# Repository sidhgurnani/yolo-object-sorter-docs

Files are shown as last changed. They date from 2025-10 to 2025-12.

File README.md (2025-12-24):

# YOLO-Based Binary Object Sorting System Documentation and Code

## Introduction/Motivation
When a bullet is fired at a crime scene it leaves behind a casing and the bullet itself. The bullet size varies depending on the gun that is being used, but each bullet contains a unique identification that can be traced back to a specific gun that it was fired with. There is currently a relatively outdated process in place, whereby an examiner will have to manually measure and identify markings. While more advanced versions of this technique can be used (standards determined by NIST), it still heavily relies on an examiner going through. While human input can be deemed necessary, it is an inefficient process that can be streamlined if the bullets were able to be somehow pre-sorted. This would save time and make the process more efficient. 
  
Designing a new device would also require engineers to justify the need for such a product, and also delve into how it can be used in other applications. There are similar existing problems in other applications. An example of such an application would be coin sorting. If there were 1000 assorted coins of differing currencies, it would be possible to sort by hand albeit through a lengthy procedure. Another example is in an agricultural setting, where one would have to maybe sort through 2-3 different types of beans efficiently. Other examples include but are not limited to: various assorted electrical components (resistors, op-amps, capacitors, etc), assorted LEGOs, and assorted perler beads. 

## Goals for this GitHub page:
The goal for this GitHub website is to provide updates about my status on this project as they had happened in real-time, including concepts that I had considered, but ultimately did not work out.

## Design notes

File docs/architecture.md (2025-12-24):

## Software Considerations

Early in the project timeline, the focus for any architectural decisions was heavily biased towards the software, as there are many possibilities for the software, and significantly fewer physical prototype solutions. 

### Early Software Decisions

Given that the project solution requires a cyberphysical system, it is best to work with some kind of microcontroller. In addition, since laptops can vary with processing power, age, graphics performance, etc, it is best to utilize a solution that is lighter on a laptop. The goal here is to have as many devices as possible be able to run the software. 

This is where the first major pathway to a solution arrives: using WebUSB. WebUSB is an API that allows certain compatible microcontrollers to be able to communicate to a web browser. This would open up the potential for users to be able to interact with the Arduino using an HTML file. Keeping this solution on a web browser would be able to allow the system to run much lighter.

Such a solution can be seen with [Google's Tiny Sorter](https://experiments.withgoogle.com/tiny-sorter/view/), which is primarily used as a teaching tool to help people learn about computer vision and sorting. One of the main drawbacks about this solution is that it doesn't accomodate for a variety of object types, and would be difficult to sort larger and heavier objects. It also does not allow a user to input a pretrained model, and instead relies on the end user to train the system. If done improperly, or in bad lighting, then the model produced is not as accurate.

This led me down a rabbit hole of using WebUSB and getting my hands on an Arduino Leonardo, which is a WebUSB-compatible Arduino. My findings about WebUSB are laid out in more detail [here](WebUSB_Findings.md). Note that this page can also be found by navigating via the development section, so you can view it then as well.

Long story short, WebUSB is not ideal (from a simplicity point of view) due to the communication protocol that needs to be put in place. With any webpage, a client and server is needed. However, this communication would have to be extended to the Arduino as well. With a large amount of communication happening between the user, client, server, and Arduino, there is bound to be a loss of data somewhere due to data being sent and recieved from multiple sources, essentially overloading the system. While the ideal scenario would be to run something like this, my prototype will not be using a web-based system to reduce the complexity of communicating information. 

### Final Software Decisions

Based on the information outlined above, I have chosen to run the program locally. A graphical user interface (GUI) will be built via Python, which will also handle communication to and from the Arduino via a serial communication port. 

The GUI will allow the user to dictate what gets done and when as well as monitor the whole system and provide that information to the user. A GUI can be constructed in many ways, however, I have chosen to use tkinter for Python. 

Communication to and from the Arduino via a serial communication port is a good option as it allows data to be sent to and from using one channel, whereas using WebUSB would mean data has to transfer from client to server to Arduino. 

More technical details can be seen on the development pages, where the software versions are outlined as I iterate through them towards a working solution. 

## Prototype Considerations

### Early Prototype Decisions

Early on, the choice had to be made to decide whether to design a prototype that works well with one kind of object or womething that won't work as well but can support a varierty of objects. 

Initially, I thought about going with the former. Coins are something that a lot of people have at their homes, including myself, and I thought testing using that would be great. I had initially wanted to design a system that works really well with coins, but coins only. However, it is more ideal to use a system that can support a variety of objects, even at reduced ability and capacity, as it allows for a proper proof of concept to be established with a relatively universal solution.

There are more things that need to be figured out before designing any prototype:

* How are objects fed into system?
* What happens if the user cannot feed objects one-by-one? How does the system handle this?
* How can the system detect the objects in a webcam? Should a box be built around the webcam and an LED to illuminate it or is there another solution?
* What mode of movement should objects use when sending an object to the webcam and from the webcam to the bin?
* etc...

### Final Prototype Decisions

Here are some answers to some of the questions I posed above:

* **How are objects fed into system?** &rarr; They can be fed one by one or ideally, through some kind of feeder, either vibration based or centrifugal.
* **What happens if the user cannot feed objects one-by-one? How does the system handle this?** &rarr; Using something like a feeder can allow objects to be fed more uniformly, regardless of how the user would load the objects.
* **How can the system detect the objects in a webcam? Should a box be built around the webcam and an LED to illuminate it or is there another solution?** &rarr; Two options can be considered: 1. creating a custom enclosure around the webcam with a light that will hopefully detect objects, or 2. using a mirror to angle the view of the webcam downward and create a 3D printed conveyor belt. 
* **What mode of movement should objects use when sending an object to the webcam and from the webcam to the bin?** &rarr; Two options can be considered: 1. Using a relatively universal rail that could transfer objects via a rail 2. perhaps this can be done with a 3D printed conveyor belt, with bins being put on the side of the conveyor belt for easy object sorting via motors or something built into the belt itself.

Update (Nov 2025):

* Note that I answered the questions with what concepts I had in mind at that time, which did not line up 100% with the concept that I ended up going with. The questions and answers were more posed to generate thinking on my side. The answers to the questions were nonbinding at the time, and ended up differing from what the final prototype looked like.

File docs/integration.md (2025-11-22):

As with any cyber physical system, the integration between the software and hardware used is very crucial. Most of the integration took place in parallel with the development, as the Arduino was a key part of the software development. This section will focus on the bridge between the software and the hardware, which is the YOLO model itself.

Technically speaking, there are a few items which can be seen as connecting a physical device to the software. The serial communication protocol and the USB cable are just two such examples. However, the item that makes or breaks how well this entire system works is the YOLO model.

I initially thought that the system was 'plug and play', however, that could not be further from the truth, which is why I have a dedicated page on training models for this system. Note that it has some general training information for all YOLO models, but it is written with this project in mind.

Another page is dedicated to troubleshooting. If one chooses to replicate this project and faces issues, refer to the troubleshooting guide to work through some of the issues. Note that all issues may not be encompassed as I was the main end user of this prototype, so I could not replicate all issues.

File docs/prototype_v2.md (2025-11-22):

The focus for this page will be new concept path that I am going down. As a reminder, below is the concept image I had drafted when decided to go down this path of development (Note that this is the same one that appears on the Prototype Development Main Page): 

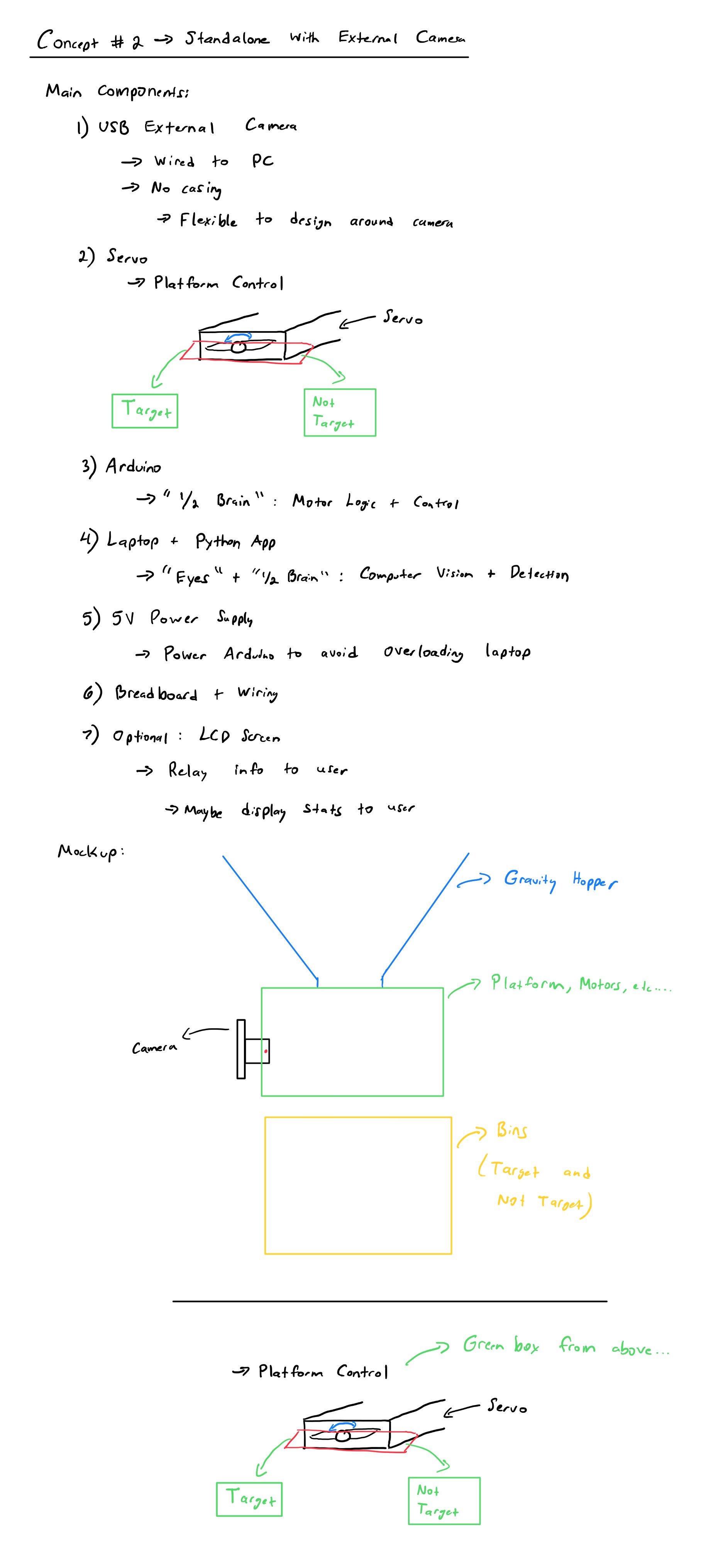
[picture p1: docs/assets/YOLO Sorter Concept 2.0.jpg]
Concept Sketch for Version 2.X


Note that there are a few changes from the concept image to the prototype:

1. **No inclusion of a gravity hopper:** As mentioned a few times across the documentation, object feeding can be considered more of a feature that is nice to have, rather than a requirement for the prototype. In addition, developing a system to feed any kind of objects that have the same relative volume is something more challenging than initially expected. Thus, it makes the most sense to focus on the object detection and sorting more than the feeding into the system, as objects can be manually fed.

2. **LCD Screen is included:** Above, an LCD screen was listed as an optional feature, however, I have decided to include it on the design. One thing to note is that the LCD working is considered lower priority as it is not important to have that working for the prototype to work.

3. **Camera Orientation:** On the concept image, the camera orientation is mounted such that objects would fall into view from up to down and along gravity and the camera would be mounted somewhere on the side to be able to see the object. Upon further reflection, it makes more sense to have the camera be top mounted. This is down to the fact that flat objects such as coins can be made more visible from above, and it won't impact the camera's ability to view other classes of objects. In hindsight, this orientation change helped, as the camera sourced for this project is very zoomed in and has a narrow FOV, which meant I had to mount the camera about 7 inches from the viewing platform. This would not have been possible if I had mounted the camera to face sideways instead of looking down at the objects. 

## Version 2.1

Below is a table of components (not including those in CAD) that need to be integrated. Note that prices are listed in USD and are reflective of those found in early October 2025. 

| Component | Picture | Estimated Unit Cost (on Amazon) |
|---|---|---|
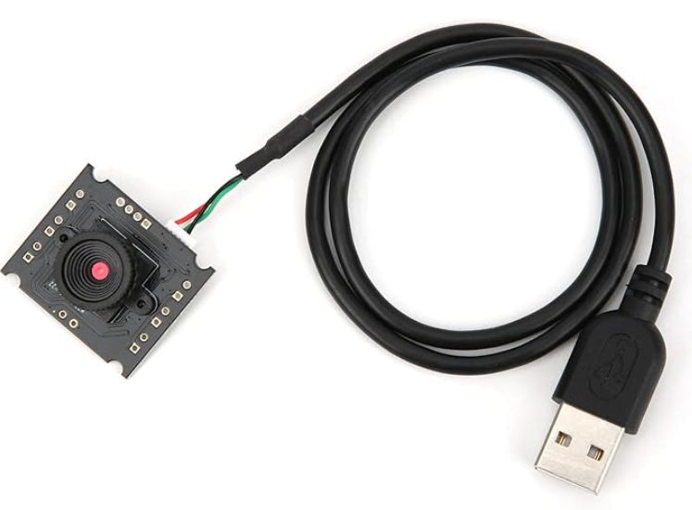
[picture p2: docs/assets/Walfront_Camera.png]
| Walfront USB Camera Module, HBV-W202012HD |  | ~$11-12 |
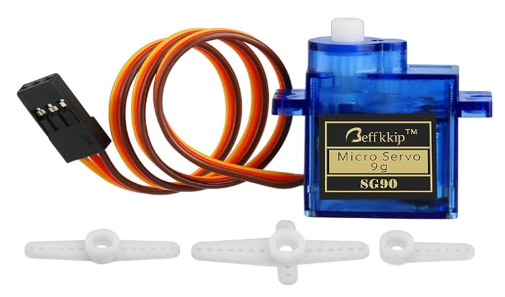
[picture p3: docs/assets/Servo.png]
| MicroServo 9G (SG90) |  | ~$2 (comes in a 4 pack for ~$8) |
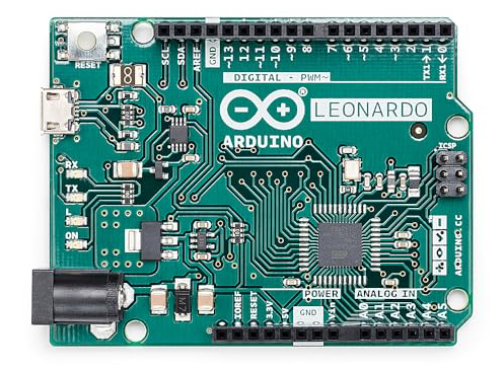
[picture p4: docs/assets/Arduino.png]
| Arduino Leonardo<br/> (**NOTE:** Any microcontroller can be used as long as it meets your requirements) |  | ~$25 | 
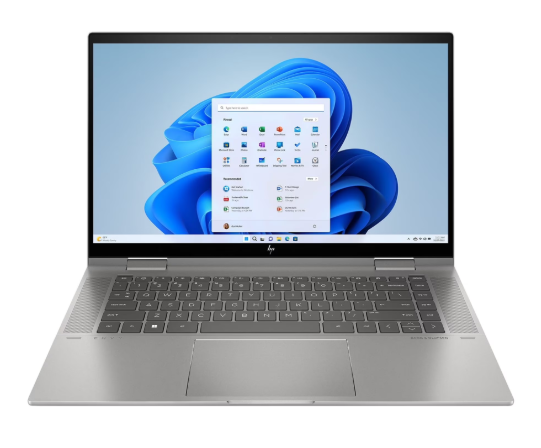
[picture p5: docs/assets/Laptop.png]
| Laptop<br/> (**NOTE:** Laptop must be able to run Python and YOLO, which requires either a decently strong CPU and/or a dedicated GPU. I have the HP ENVY x360 2-in-1 Laptop 15-ew1xxx.)<br/> See Geekbench [here](https://browser.geekbench.com/v5/cpu/22137005) for detailed info about my laptop's specs. |  | ~$800 | 
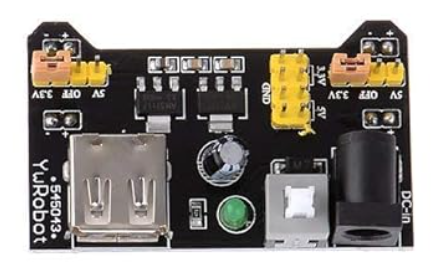
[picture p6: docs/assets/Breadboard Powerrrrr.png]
| 3.3V/5V Breadboard Power Supply Module |  | ~$1.80 (comes in a 5 pack for ~9) | 
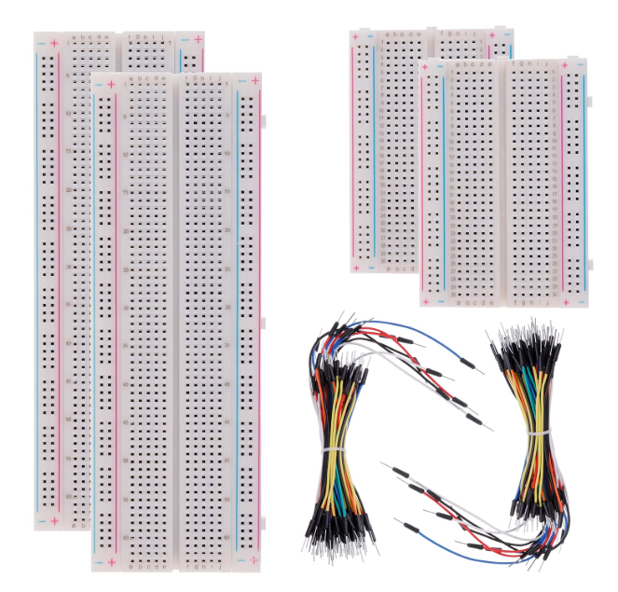
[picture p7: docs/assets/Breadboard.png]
| Breadboard and Jumper Cables (and LEDs if desired) |  | ~$10 (for full pack as pictured) | 
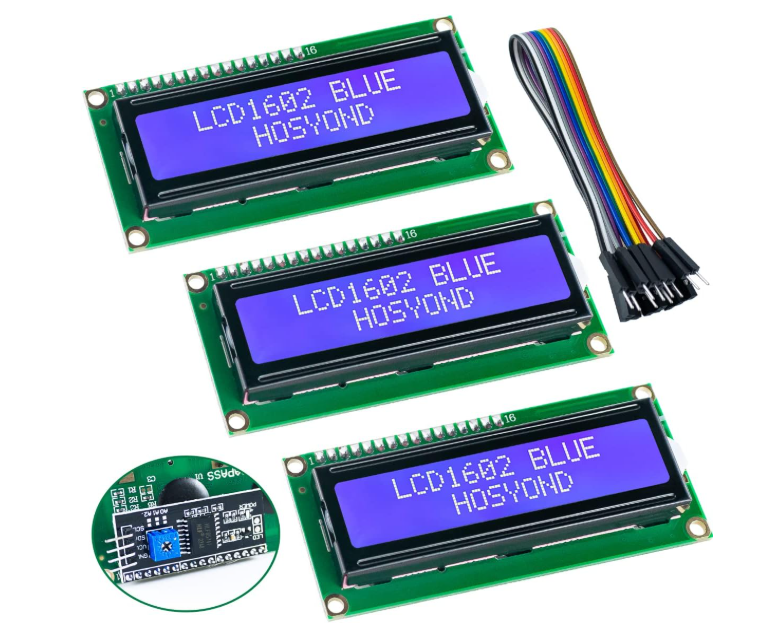
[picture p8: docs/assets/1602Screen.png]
| 1602 LCD Screen |  | ~$4.33 (comes in a 3 pack for ~$13) | 
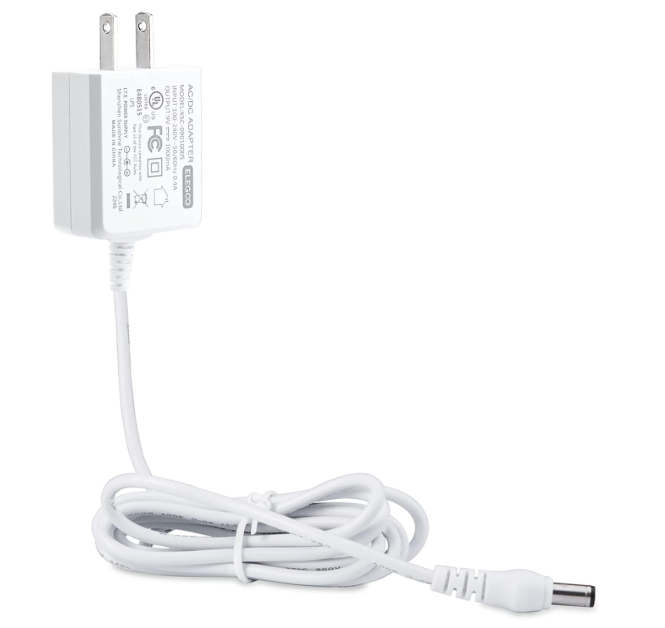
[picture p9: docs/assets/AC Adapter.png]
| AC Adapter (9V, 1A Output) |  | ~$8 | 

### Arduino/Microcontroller Pin Usage

An Arduino Leonardo has a total of 12 Digital Pins (7 of which are PWM) and 6 Analog Pins. Before thinking about the CAD, it is important to see how many pins are used for what is listed above. This provides a good baseline and is able to inform future improvements. 

[Click to view a great article that details information about the Arduino Leonardo and its pins.](https://www.etechnophiles.com/leonardo-pinout-schematic-and-specifications/)

| Electrical Component | Description | Pins required on Arduino |
|---|---|---|
| Green LED | Lets user know that an object can be fed into the system for sorting | 1 Digital PWM Pin |
| Red LED | Lets user know that an object can NOT be fed into the system for sorting | 1 Digital PWM Pin |
| Servo | Rotates platform to send object to target or not target bin | 1 Digital PWM Pin | 
| LCD Screen | Lets user know status of system without having to look at Python interface; Displays stats to user at the end of sorting session | 6 Digital Pins |

One of the things I was initially considering was including a gate to physically stop objects from being fed, however that is not necessary on the prototype. Ultimately, I picked including a screen over a gate, due to constraints on pins. This can be considered another improvement that would be nice to have. 

Since most of the pins left are analog pins, this leaves room to include any sensors that may be needed should the information from the camera not be enough for the system to work properly.

### CAD

I used Onshape to create the CAD for this prototype, and you can view the CAD by clicking [here](https://cad.onshape.com/documents/56ded4b8e86468a67475ca0c/w/01bca40152a05fd67c7a1a53/e/aa33980481ab51f746d18740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).

**Picture Galleries of CAD:**

Various galleries are below to show more details about the components and subassemblies of the CAD. Click thumbnail to enlarge the images.

Camera Mounting Subassembly: 

<!-- Lightbox overlay for Gallery 1 -->
<div id="lightbox1" style="display:none; position:fixed; top:0; left:0; width:100%; height:100%;
  background: rgba(0,0,0,0.9); justify-content:center; align-items:center; z-index:1000; flex-direction: column;">
  <button id="prevBtn1" style="position:absolute; left:20px; top:50%; transform:translateY(-50%); color:white; font-size:2rem; background:none; border:none; cursor:pointer;">&#10094;</button>
  
  <div id="caption1" style="color:white; margin-top:20px; text-align:center; max-width:80%; padding:0 20px;">
    <h3 id="title1" style="margin:10px 0; font-size:1.5rem;"></h3>
    
  </div>
  <button id="nextBtn1" style="position:absolute; right:20px; top:50%; transform:translateY(-50%); color:white; font-size:2rem; background:none; border:none; cursor:pointer;">&#10095;</button>
  <button id="closeBtn1" style="position:absolute; top:20px; right:30px; color:white; font-size:2rem; background:none; border:none; cursor:pointer;">&times;</button>
</div>

<style>
  #gallery1 img.thumb, #gallery2 img.thumb, #gallery3 img.thumb, #gallery4 img.thumb {
    width: 100%;
    height: auto;
    max-width: 200px;
    min-width: 150px;
    cursor: pointer;
    border-radius: 6px;
    transition: transform 0.2s;
    object-fit: cover;
    aspect-ratio: 4/3;
  }

  #gallery1 img.thumb:hover, #gallery2 img.thumb:hover, #gallery3 img.thumb:hover, #gallery4 img.thumb:hover {
    transform: scale(1.05);
  }

  @media (max-width: 600px) {
    #gallery1 img.thumb, #gallery2 img.thumb, #gallery3 img.thumb, #gallery4 img.thumb {
      max-width: calc(50% - 5px);
    }
    #lightbox1 img, #lightbox2 img, #lightbox3 img, #lightbox4 img {
      max-width: 95% !important;
      max-height: 60% !important;
    }
  }

  #prevBtn1, #nextBtn1, #closeBtn1, #prevBtn2, #nextBtn2, #closeBtn2, 
  #prevBtn3, #nextBtn3, #closeBtn3, #prevBtn4, #nextBtn4, #closeBtn4 {
    user-select: none;
  }

  #prevBtn1:hover, #nextBtn1:hover, #closeBtn1:hover,
  #prevBtn2:hover, #nextBtn2:hover, #closeBtn2:hover,
  #prevBtn3:hover, #nextBtn3:hover, #closeBtn3:hover,
  #prevBtn4:hover, #nextBtn4:hover, #closeBtn4:hover {
    opacity: 0.7;
  }
</style>

<script>
document.addEventListener("DOMContentLoaded", () => {
    const galleryDiv1 = document.getElementById('gallery1');
    const lightbox1 = document.getElementById('lightbox1');
    const lightboxImg1 = document.getElementById('lightbox-img1');
    const prevBtn1 = document.getElementById('prevBtn1');
    const nextBtn1 = document.getElementById('nextBtn1');
    const closeBtn1 = document.getElementById('closeBtn1');
    const title1 = document.getElementById('title1');
    const desc1 = document.getElementById('desc1');

    // MODIFY THIS: Add your images with titles and captions
    const images1 = [
        {
            src: "../assets/2.1_Camera_1.png",
            title: "Camera Frame Corner Sleeve (1 of 2)",
            caption: "Four are required. Mounts to top and allows camera frame to slide in and out."
        },
        {
            src: "../assets/2.1_Camera_2.png",
            title: "Camera Frame Corner Sleeve (2 of 2)",
            caption: "Four are required. Mounts to top and allows camera frame to slide in and out."
        },
        {
            src: "../assets/2.1_Camera_Frame_1.png",
            title: "Camera Frame (1 of 5)",
            caption: "Keeps camera steady around 7 inches above viewing platform, with hole to allow lens to go through."
        }, 
        {
            src: "../assets/2.1_Camera_Frame_2.png",
            title: "Camera Frame (2 of 5)",
            caption: "Keeps camera steady around 7 inches above viewing platform, with hole to allow lens to go through."
        }, 
        {
            src: "../assets/2.1_Camera_Frame_3.png",
            title: "Camera Frame (3 of 5)",
            caption: "Keeps camera steady around 7 inches above viewing platform, with hole to allow lens to go through."
        }, 
        {
            src: "../assets/2.1_Camera_Frame_4.png",
            title: "Camera Frame (4 of 5)",
            caption: "Keeps camera steady around 7 inches above viewing platform, with hole to allow lens to go through."
        }, 
        {
            src: "../assets/2.1_Camera_Frame_5.png",
            title: "Camera Frame (5 of 5)",
            caption: "Keeps camera steady around 7 inches above viewing platform, with hole to allow lens to go through."
        },
        {
            src: "../assets/2.1_Top_Plate_1.png",
            title: "Top Plate (1 of 3)",
            caption: "Screws onto frame to hold camera in place. Features a channel for the wired connection to go through."
        }, 
        {
            src: "../assets/2.1_Top_Plate_2.png",
            title: "Top Plate (2 of 3)",
            caption: "Screws onto frame to hold camera in place. Features a channel for the wired connection to go through."
        }, 
        {
            src: "../assets/2.1_Top_Plate_3.png",
            title: "Top Plate (3 of 3)",
            caption: "Screws onto frame to hold camera in place. Features a channel for the wired connection to go through."
        },
        {
            src: "../assets/2.1_Camera_Assembly_1.png",
            title: "Camera Mounting Subassembly (1 of 5)",
            caption: "Camera Mounting Subassembly. Mounted on top of prototype."
        },
        {
            src: "../assets/2.1_Camera_Assembly_2.png",
            title: "Camera Mounting Subassembly (2 of 5)",
            caption: "Camera Mounting Subassembly. Mounted on top of prototype."
        },
        {
            src: "../assets/2.1_Camera_Assembly_3.png",
            title: "Camera Mounting Subassembly (3 of 5)",
            caption: "Camera Mounting Subassembly. Mounted on top of prototype."
        },
        {
            src: "../assets/2.1_Camera_Assembly_4.png",
            title: "Camera Mounting Subassembly (4 of 5)",
            caption: "Camera Mounting Subassembly. Mounted on top of prototype."
        },
        {
            src: "../assets/2.1_Camera_Assembly_5.png",
            title: "Camera Mounting Subassembly (5 of 5)",
            caption: "Camera Mounting Subassembly. Mounted on top of prototype."
        }
    ];

    let currentIndex1 = 0;

    // Load thumbnails
    images1.forEach((img, i) => {
        const thumb = document.createElement('img');
        thumb.src = img.src;
        thumb.className = 'thumb';
        thumb.onclick = () => openLightbox1(i);
        galleryDiv1.appendChild(thumb);
    });

    function openLightbox1(index) {
        currentIndex1 = index;
        lightbox1.style.display = "flex";
        lightboxImg1.src = images1[currentIndex1].src;
        title1.textContent = images1[currentIndex1].title;
        desc1.textContent = images1[currentIndex1].caption;
    }

    function closeLightbox1() {
        lightbox1.style.display = "none";
    }

    function showNext1() {
        currentIndex1 = (currentIndex1 + 1) % images1.length;
        lightboxImg1.src = images1[currentIndex1].src;
        title1.textContent = images1[currentIndex1].title;
        desc1.textContent = images1[currentIndex1].caption;
    }

    function showPrev1() {
        currentIndex1 = (currentIndex1 - 1 + images1.length) % images1.length;
        lightboxImg1.src = images1[currentIndex1].src;
        title1.textContent = images1[currentIndex1].title;
        desc1.textContent = images1[currentIndex1].caption;
    }

    // Navigation
    nextBtn1.onclick = (e) => { e.stopPropagation(); showNext1(); };
    prevBtn1.onclick = (e) => { e.stopPropagation(); showPrev1(); };
    closeBtn1.onclick = closeLightbox1;

    // Close on background click
    lightbox1.onclick = (e) => {
        if (e.target === lightbox1) closeLightbox1();
    };

    // Keyboard controls
    document.addEventListener('keydown', (e) => {
        if (lightbox1.style.display === "flex") {
            if (e.key === "ArrowRight") showNext1();
            if (e.key === "ArrowLeft") showPrev1();
            if (e.key === "Escape") closeLightbox1();
        }
    });
});
</script>

<div><br></div>

Sorting System Subassembly: 

<!-- Lightbox overlay for Gallery 2 -->
<div id="lightbox2" style="display:none; position:fixed; top:0; left:0; width:100%; height:100%;
  background: rgba(0,0,0,0.9); justify-content:center; align-items:center; z-index:1000; flex-direction: column;">
  <button id="prevBtn2" style="position:absolute; left:20px; top:50%; transform:translateY(-50%); color:white; font-size:2rem; background:none; border:none; cursor:pointer;">&#10094;</button>
  
  <div id="caption2" style="color:white; margin-top:20px; text-align:center; max-width:80%; padding:0 20px;">
    <h3 id="title2" style="margin:10px 0; font-size:1.5rem;"></h3>
    
  </div>
  <button id="nextBtn2" style="position:absolute; right:20px; top:50%; transform:translateY(-50%); color:white; font-size:2rem; background:none; border:none; cursor:pointer;">&#10095;</button>
  <button id="closeBtn2" style="position:absolute; top:20px; right:30px; color:white; font-size:2rem; background:none; border:none; cursor:pointer;">&times;</button>
</div>

<script>
document.addEventListener("DOMContentLoaded", () => {
    const galleryDiv2 = document.getElementById('gallery2');
    const lightbox2 = document.getElementById('lightbox2');
    const lightboxImg2 = document.getElementById('lightbox-img2');
    const prevBtn2 = document.getElementById('prevBtn2');
    const nextBtn2 = document.getElementById('nextBtn2');
    const closeBtn2 = document.getElementById('closeBtn2');
    const title2 = document.getElementById('title2');
    const desc2 = document.getElementById('desc2');

    // MODIFY THIS: Add your images with titles and captions
    const images2 = [
        {
            src: "../assets/2.1_Sorting_Cup_1.png",
            title: "Cup (1 of 2)",
            caption: "In CAD for modelling purposes only. Actual cup used is a styrofoam coffee cup with an approx capacity of 12-14 oz."
        },
        {
            src: "../assets/2.1_Sorting_Cup_2.png",
            title: "Cup (2 of 2)",
            caption: "In CAD for modelling purposes only. Actual cup used is a styrofoam coffee cup with an approx capacity of 12-14 oz."
        },
        {
            src: "../assets/2.1_Sorting_Cup_Base_1.png",
            title: "Cup Base (1 of 4)",
            caption: "Two are required. Used to keep base of cup in place."
        }, 
        {
            src: "../assets/2.1_Sorting_Cup_Base_2.png",
            title: "Cup Base (2 of 4)",
            caption: "Two are required. Used to keep base of cup in place."
        }, 
        {
            src: "../assets/2.1_Sorting_Cup_Base_3.png",
            title: "Cup Base (3 of 4)",
            caption: "Two are required. Used to keep base of cup in place."
        }, 
        {
            src: "../assets/2.1_Sorting_Cup_Base_4.png",
            title: "Cup Base (4 of 4)",
            caption: "Two are required. Used to keep base of cup in place."
        },
        {
            src: "../assets/2.1_Sorting_Cup_Drawer_1.png",
            title: "Cup 'Drawer' (1 of 3)",
            caption: "Two are required. Slots used to slide cup back and forth to easily access and empty cup when needed. Counterbore on bottom allows nut to be recessed and not interfere with motion."
        }, 
        {
            src: "../assets/2.1_Sorting_Cup_Drawer_2.png",
            title: "Cup 'Drawer' (2 of 3)",
            caption: "Two are required. Slots used to slide cup back and forth to easily access and empty cup when needed. Counterbore on bottom allows nut to be recessed and not interfere with motion."
        }, 
        {
            src: "../assets/2.1_Sorting_Cup_Drawer_3.png",
            title: "Cup 'Drawer' (3 of 3)",
            caption: "Two are required. Slots used to slide cup back and forth to easily access and empty cup when needed. Counterbore on bottom allows nut to be recessed and not interfere with motion."
        },
        {
            src: "../assets/2.1_Sorting_Cup_Underside_Assembly_1.png",
            title: "Cup Underside Assembly (1 of 2)",
            caption: "NOTE: White 'washer' was printed to ensure bolt would hold everything together."
        }, 
        {
            src: "../assets/2.1_Sorting_Cup_Underside_Assembly_2.png",
            title: "Cup Underside Assembly (2 of 2)",
            caption: "NOTE: White 'washer' was printed to ensure bolt would hold everything together."
        },
        {
            src: "../assets/2.1_Sorting_Platform_1.png",
            title: "Platform (1 of 6)",
            caption: "Object gets fed onto platform and it rotates to either 'Target' or 'Not Target'."
        },
        {
            src: "../assets/2.1_Sorting_Platform_2.png",
            title: "Platform (2 of 6)",
            caption: "Object gets fed onto platform and it rotates to either 'Target' or 'Not Target'."
        },
        {
            src: "../assets/2.1_Sorting_Platform_3.png",
            title: "Platform (3 of 6)",
            caption: "Object gets fed onto platform and it rotates to either 'Target' or 'Not Target'."
        },
        {
            src: "../assets/2.1_Sorting_Platform_4.png",
            title: "Platform (4 of 6)",
            caption: "Object gets fed onto platform and it rotates to either 'Target' or 'Not Target'."
        },
        {
            src: "../assets/2.1_Sorting_Platform_5.png",
            title: "Platform (5 of 6)",
            caption: "Object gets fed onto platform and it rotates to either 'Target' or 'Not Target'."
        },
        {
            src: "../assets/2.1_Sorting_Platform_6.png",
            title: "Platform (6 of 6)",
            caption: "Object gets fed onto platform and it rotates to either 'Target' or 'Not Target'."
        },
        {
            src: "../assets/2.1_Sorting_Ramp_1.png",
            title: "Ramp (1 of 5)",
            caption: "Object is manually fed from top of ramp and it goes down ramp onto platform. Ramp also has a small part to house one end of the platform to ensure platform stability."
        },
        {
            src: "../assets/2.1_Sorting_Ramp_2.png",
            title: "Ramp (2 of 5)",
            caption: "Object is manually fed from top of ramp and it goes down ramp onto platform. Ramp also has a small part to house one end of the platform to ensure platform stability."
        },
        {
            src: "../assets/2.1_Sorting_Ramp_3.png",
            title: "Ramp (3 of 5)",
            caption: "Object is manually fed from top of ramp and it goes down ramp onto platform. Ramp also has a small part to house one end of the platform to ensure platform stability."
        },
        {
            src: "../assets/2.1_Sorting_Ramp_4.png",
            title: "Ramp (4 of 5)",
            caption: "Object is manually fed from top of ramp and it goes down ramp onto platform. Ramp also has a small part to house one end of the platform to ensure platform stability."
        },
        {
            src: "../assets/2.1_Sorting_Ramp_5.png",
            title: "Ramp (5 of 5)",
            caption: "Object is manually fed from top of ramp and it goes down ramp onto platform. Ramp also has a small part to house one end of the platform to ensure platform stability."
        },
        {
            src: "../assets/2.1_Sorting_Servo_Mount_1.png",
            title: "Servo Mount (1 of 5)",
            caption: "Attaches to shell and holds servo in place."
        },
        {
            src: "../assets/2.1_Sorting_Servo_Mount_2.png",
            title: "Servo Mount (2 of 5)",
            caption: "Attaches to shell and holds servo in place."
        },
        {
            src: "../assets/2.1_Sorting_Servo_Mount_3.png",
            title: "Servo Mount (3 of 5)",
            caption: "Attaches to shell and holds servo in place."
        },
        {
            src: "../assets/2.1_Sorting_Servo_Mount_4.png",
            title: "Servo Mount (4 of 5)",
            caption: "Attaches to shell and holds servo in place."
        },
        {
            src: "../assets/2.1_Sorting_Servo_Mount_5.png",
            title: "Servo Mount (5 of 5)",
            caption: "Attaches to shell and holds servo in place."
        },
        {
            src: "../assets/2.1_Sorting_Assembly_1.png",
            title: "Sorting System Subassembly (1 of 7)",
            caption: "Full sorting subassembly images."
        },
        {
            src: "../assets/2.1_Sorting_Assembly_2.png",
            title: "Sorting System Subassembly (2 of 7)",
            caption: "Full sorting subassembly images."
        },
        {
            src: "../assets/2.1_Sorting_Assembly_3.png",
            title: "Sorting System Subassembly (3 of 7)",
            caption: "Full sorting subassembly images."
        },
        {
            src: "../assets/2.1_Sorting_Assembly_4.png",
            title: "Sorting System Subassembly (4 of 7)",
            caption: "Full sorting subassembly images."
        },
        {
            src: "../assets/2.1_Sorting_Assembly_5.png",
            title: "Sorting System Subassembly (5 of 7)",
            caption: "Full sorting subassembly images."
        },
        {
            src: "../assets/2.1_Sorting_Assembly_6.png",
            title: "Sorting System Subassembly (6 of 7)",
            caption: "Full sorting subassembly images."
        },
        {
            src: "../assets/2.1_Sorting_Assembly_7.png",
            title: "Sorting System Subassembly (7 of 7)",
            caption: "Closeup of Platform and how end sits inside ramp."
        },
    ];

    let currentIndex2 = 0;

    // Load thumbnails
    images2.forEach((img, i) => {
        const thumb = document.createElement('img');
        thumb.src = img.src;
        thumb.className = 'thumb';
        thumb.onclick = () => openLightbox2(i);
        galleryDiv2.appendChild(thumb);
    });

    function openLightbox2(index) {
        currentIndex2 = index;
        lightbox2.style.display = "flex";
        lightboxImg2.src = images2[currentIndex2].src;
        title2.textContent = images2[currentIndex2].title;
        desc2.textContent = images2[currentIndex2].caption;
    }

    function closeLightbox2() {
        lightbox2.style.display = "none";
    }

    function showNext2() {
        currentIndex2 = (currentIndex2 + 1) % images2.length;
        lightboxImg2.src = images2[currentIndex2].src;
        title2.textContent = images2[currentIndex2].title;
        desc2.textContent = images2[currentIndex2].caption;
    }

    function showPrev2() {
        currentIndex2 = (currentIndex2 - 1 + images2.length) % images2.length;
        lightboxImg2.src = images2[currentIndex2].src;
        title2.textContent = images2[currentIndex2].title;
        desc2.textContent = images2[currentIndex2].caption;
    }

    // Navigation
    nextBtn2.onclick = (e) => { e.stopPropagation(); showNext2(); };
    prevBtn2.onclick = (e) => { e.stopPropagation(); showPrev2(); };
    closeBtn2.onclick = closeLightbox2;

    // Close on background click
    lightbox2.onclick = (e) => {
        if (e.target === lightbox2) closeLightbox2();
    };

    // Keyboard controls
    document.addEventListener('keydown', (e) => {
        if (lightbox2.style.display === "flex") {
            if (e.key === "ArrowRight") showNext2();
            if (e.key === "ArrowLeft") showPrev2();
            if (e.key === "Escape") closeLightbox2();
        }
    });
});
</script>

<div><br></div>

Body Subassembly:

<!-- Lightbox overlay for Gallery 3 -->
<div id="lightbox3" style="display:none; position:fixed; top:0; left:0; width:100%; height:100%;
  background: rgba(0,0,0,0.9); justify-content:center; align-items:center; z-index:1000; flex-direction: column;">
  <button id="prevBtn3" style="position:absolute; left:20px; top:50%; transform:translateY(-50%); color:white; font-size:2rem; background:none; border:none; cursor:pointer;">&#10094;</button>
  
  <div id="caption3" style="color:white; margin-top:20px; text-align:center; max-width:80%; padding:0 20px;">
    <h3 id="title3" style="margin:10px 0; font-size:1.5rem;"></h3>
    
  </div>
  <button id="nextBtn3" style="position:absolute; right:20px; top:50%; transform:translateY(-50%); color:white; font-size:2rem; background:none; border:none; cursor:pointer;">&#10095;</button>
  <button id="closeBtn3" style="position:absolute; top:20px; right:30px; color:white; font-size:2rem; background:none; border:none; cursor:pointer;">&times;</button>
</div>

<script>
document.addEventListener("DOMContentLoaded", () => {
    const galleryDiv3 = document.getElementById('gallery3');
    const lightbox3 = document.getElementById('lightbox3');
    const lightboxImg3 = document.getElementById('lightbox-img3');
    const prevBtn3 = document.getElementById('prevBtn3');
    const nextBtn3 = document.getElementById('nextBtn3');
    const closeBtn3 = document.getElementById('closeBtn3');
    const title3 = document.getElementById('title3');
    const desc3 = document.getElementById('desc3');

    // MODIFY THIS: Add your images with titles and captions
    const images3 = [
        {
            src: "../assets/2.1_Body_Base_1.png",
            title: "Base (1 of 3)",
            caption: "Provides extra rigidity to overall prototype. Nut sticking out from bottom will go into couterbore holes to allow system to be flush."
        },
        {
            src: "../assets/2.1_Body_Base_2.png",
            title: "Base (2 of 3)",
            caption: "Provides extra rigidity to overall prototype. Nut sticking out from bottom will go into couterbore holes to allow system to be flush."
        },
        {
            src: "../assets/2.1_Body_Base_3.png",
            title: "Base (3 of 3)",
            caption: "Provides extra rigidity to overall prototype. Nut sticking out from bottom will go into couterbore holes to allow system to be flush."
        },
        {
            src: "../assets/2.1_Body_Bottom_1.png",
            title: "Bottom (1 of 3)",
            caption: "Provides mounting points for shell and provides pins for pin-slot mechanism to allow cup 'drawers' to move."
        },
        {
            src: "../assets/2.1_Body_Bottom_2.png",
            title: "Bottom (2 of 3)",
            caption: "Provides mounting points for shell and provides pins for pin-slot mechanism to allow cup 'drawers' to move."
        },
        {
            src: "../assets/2.1_Body_Bottom_3.png",
            title: "Bottom (3 of 3)",
            caption: "Provides mounting points for shell and provides pins for pin-slot mechanism to allow cup 'drawers' to move."
        },
        {
            src: "../assets/2.1_Body_Labels_1.png",
            title: "Bin Label Plates (1 of 1)",
            caption: "Two are used, remain optional to design. Labels bin to avoid confusion. NOTE: Text for labels was added in Bambu Studio (slicing software) and .3mf file is provided later on this page."
        },
        {
            src: "../assets/2.1_Body_LCD_Holder_1.png",
            title: "LCD Screen Frame (1 of 3)",
            caption: "Mounts LCD Screen to shell and provides space to accomodate green and red LEDs."
        },
        {
            src: "../assets/2.1_Body_LCD_Holder_2.png",
            title: "LCD Screen Frame (2 of 3)",
            caption: "Mounts LCD Screen to shell and provides space to accomodate green and red LEDs."
        },
        {
            src: "../assets/2.1_Body_LCD_Holder_3.png",
            title: "LCD Screen Frame (3 of 3)",
            caption: "Mounts LCD Screen to shell and provides space to accomodate green and red LEDs."
        },
        {
            src: "../assets/2.1_Body_Shell_1.png",
            title: "Shell (1 of 7)",
            caption: "Provides height to system, mounting points, and wire routing for servo wires."
        },
        {
            src: "../assets/2.1_Body_Shell_2.png",
            title: "Shell (2 of 7)",
            caption: "Provides height to system, mounting points, and wire routing for servo wires."
        },
        {
            src: "../assets/2.1_Body_Shell_3.png",
            title: "Shell (3 of 7)",
            caption: "Provides height to system, mounting points, and wire routing for servo wires."
        },
        {
            src: "../assets/2.1_Body_Shell_4.png",
            title: "Shell (4 of 7)",
            caption: "Provides height to system, mounting points, and wire routing for servo wires."
        },
        {
            src: "../assets/2.1_Body_Shell_5.png",
            title: "Shell (5 of 7)",
            caption: "Provides height to system, mounting points, and wire routing for servo wires."
        },
        {
            src: "../assets/2.1_Body_Shell_6.png",
            title: "Shell (6 of 7)",
            caption: "Provides height to system, mounting points, and wire routing for servo wires."
        },
        {
            src: "../assets/2.1_Body_Shell_7.png",
            title: "Shell (7 of 7)",
            caption: "Provides height to system, mounting points, and wire routing for servo wires."
        },
        {
            src: "../assets/2.1_Body_Assembly_1.png",
            title: "Body Subassembly (1 of 7)",
            caption: "Pictures of fully assembled body in CAD."
        },
        {
            src: "../assets/2.1_Body_Assembly_2.png",
            title: "Body Subassembly (2 of 7)",
            caption: "Pictures of fully assembled body in CAD."
        },
        {
            src: "../assets/2.1_Body_Assembly_3.png",
            title: "Body Subassembly (3 of 7)",
            caption: "Pictures of fully assembled body in CAD."
        },
        {
            src: "../assets/2.1_Body_Assembly_4.png",
            title: "Body Subassembly (4 of 7)",
            caption: "Pictures of fully assembled body in CAD."
        },
        {
            src: "../assets/2.1_Body_Assembly_5.png",
            title: "Body Subassembly (5 of 7)",
            caption: "Pictures of fully assembled body in CAD."
        },
        {
            src: "../assets/2.1_Body_Assembly_6.png",
            title: "Body Subassembly (6 of 7)",
            caption: "Pictures of fully assembled body in CAD."
        },
        {
            src: "../assets/2.1_Body_Assembly_7.png",
            title: "Body Subassembly (7 of 7)",
            caption: "Pictures of fully assembled body in CAD."
        }
    ];

    let currentIndex3 = 0;

    // Load thumbnails
    images3.forEach((img, i) => {
        const thumb = document.createElement('img');
        thumb.src = img.src;
        thumb.className = 'thumb';
        thumb.onclick = () => openLightbox3(i);
        galleryDiv3.appendChild(thumb);
    });

    function openLightbox3(index) {
        currentIndex3 = index;
        lightbox3.style.display = "flex";
        lightboxImg3.src = images3[currentIndex3].src;
        title3.textContent = images3[currentIndex3].title;
        desc3.textContent = images3[currentIndex3].caption;
    }

    function closeLightbox3() {
        lightbox3.style.display = "none";
    }

    function showNext3() {
        currentIndex3 = (currentIndex3 + 1) % images3.length;
        lightboxImg3.src = images3[currentIndex3].src;
        title3.textContent = images3[currentIndex3].title;
        desc3.textContent = images3[currentIndex3].caption;
    }

    function showPrev3() {
        currentIndex3 = (currentIndex3 - 1 + images3.length) % images3.length;
        lightboxImg3.src = images3[currentIndex3].src;
        title3.textContent = images3[currentIndex3].title;
        desc3.textContent = images3[currentIndex3].caption;
    }

    // Navigation
    nextBtn3.onclick = (e) => { e.stopPropagation(); showNext3(); };
    prevBtn3.onclick = (e) => { e.stopPropagation(); showPrev3(); };
    closeBtn3.onclick = closeLightbox3;

    // Close on background click
    lightbox3.onclick = (e) => {
        if (e.target === lightbox3) closeLightbox3();
    };

    // Keyboard controls
    document.addEventListener('keydown', (e) => {
        if (lightbox3.style.display === "flex") {
            if (e.key === "ArrowRight") showNext3();
            if (e.key === "ArrowLeft") showPrev3();
            if (e.key === "Escape") closeLightbox3();
        }
    });
});
</script>

<div><br></div>

Full Assembly: 

<!-- Lightbox overlay for Gallery 4 -->
<div id="lightbox4" style="display:none; position:fixed; top:0; left:0; width:100%; height:100%;
  background: rgba(0,0,0,0.9); justify-content:center; align-items:center; z-index:1000; flex-direction: column;">
  <button id="prevBtn4" style="position:absolute; left:20px; top:50%; transform:translateY(-50%); color:white; font-size:2rem; background:none; border:none; cursor:pointer;">&#10094;</button>
  
  <div id="caption4" style="color:white; margin-top:20px; text-align:center; max-width:80%; padding:0 20px;">
    <h3 id="title4" style="margin:10px 0; font-size:1.5rem;"></h3>
    
  </div>
  <button id="nextBtn4" style="position:absolute; right:20px; top:50%; transform:translateY(-50%); color:white; font-size:2rem; background:none; border:none; cursor:pointer;">&#10095;</button>
  <button id="closeBtn4" style="position:absolute; top:20px; right:30px; color:white; font-size:2rem; background:none; border:none; cursor:pointer;">&times;</button>
</div>

<script>
document.addEventListener("DOMContentLoaded", () => {
    const galleryDiv4 = document.getElementById('gallery4');
    const lightbox4 = document.getElementById('lightbox4');
    const lightboxImg4 = document.getElementById('lightbox-img4');
    const prevBtn4 = document.getElementById('prevBtn4');
    const nextBtn4 = document.getElementById('nextBtn4');
    const closeBtn4 = document.getElementById('closeBtn4');
    const title4 = document.getElementById('title4');
    const desc4 = document.getElementById('desc4');

    // MODIFY THIS: Add your images with titles and captions
    const images4 = [
        {
            src: "../assets/2.1_Full_2.png",
            title: "Full Assembly of Version 2.1 (1 of 5)",
            caption: "Fully assembled version in CAD with semi-accurate color to filament being used to 3D print it."
        },
        {
            src: "../assets/2.1_Full_3.png",
            title: "Full Assembly of Version 2.1 (2 of 5)",
            caption: "Fully assembled version in CAD with semi-accurate color to filament being used to 3D print it."
        },
        {
            src: "../assets/2.1_Full_4.png",
            title: "Full Assembly of Version 2.1 (3 of 5)",
            caption: "Fully assembled version in CAD with semi-accurate color to filament being used to 3D print it."
        },
        {
            src: "../assets/2.1_Full_5.png",
            title: "Full Assembly of Version 2.1 (4 of 5)",
            caption: "Fully assembled version in CAD with semi-accurate color to filament being used to 3D print it."
        },
        {
            src: "../assets/2.1_Full_1.png",
            title: "Full Assembly of Version 2.1 (5 of 5)",
            caption: "Fully assembled version in CAD with semi-accurate color to filament being used to 3D print it."
        }
    ];

    let currentIndex4 = 0;

    // Load thumbnails
    images4.forEach((img, i) => {
        const thumb = document.createElement('img');
        thumb.src = img.src;
        thumb.className = 'thumb';
        thumb.onclick = () => openLightbox4(i);
        galleryDiv4.appendChild(thumb);
    });

    function openLightbox4(index) {
        currentIndex4 = index;
        lightbox4.style.display = "flex";
        lightboxImg4.src = images4[currentIndex4].src;
        title4.textContent = images4[currentIndex4].title;
        desc4.textContent = images4[currentIndex4].caption;
    }

    function closeLightbox4() {
        lightbox4.style.display = "none";
    }

    function showNext4() {
        currentIndex4 = (currentIndex4 + 1) % images4.length;
        lightboxImg4.src = images4[currentIndex4].src;
        title4.textContent = images4[currentIndex4].title;
        desc4.textContent = images4[currentIndex4].caption;
    }

    function showPrev4() {
        currentIndex4 = (currentIndex4 - 1 + images4.length) % images4.length;
        lightboxImg4.src = images4[currentIndex4].src;
        title4.textContent = images4[currentIndex4].title;
        desc4.textContent = images4[currentIndex4].caption;
    }

    // Navigation
    nextBtn4.onclick = (e) => { e.stopPropagation(); showNext4(); };
    prevBtn4.onclick = (e) => { e.stopPropagation(); showPrev4(); };
    closeBtn4.onclick = closeLightbox4;

    // Close on background click
    lightbox4.onclick = (e) => {
        if (e.target === lightbox4) closeLightbox4();
    };

    // Keyboard controls
    document.addEventListener('keydown', (e) => {
        if (lightbox4.style.display === "flex") {
            if (e.key === "ArrowRight") showNext4();
            if (e.key === "ArrowLeft") showPrev4();
            if (e.key === "Escape") closeLightbox4();
        }
    });
});
</script>

<div><br></div>

### Prototype Production

A total of 5 colors were used throughout the printing process. I am listing the color as well as the brand and type of filament.

1. White (Bambu Lab PLA Basic)
2. Black (Bambu Lab PLA Basic)
3. Light Grey (Bambu Lab PLA Basic)
4. Transparent Red (SUNLU Transparent PLA)
5. Transparent Blue (SUNLU Transparent PLA)

Most of the slicing settings are pretty much left untouched, however, there are some notable settings that I used:

* **Infill Pattern:** Gyroid
* **Infill Density:** 15% (can probably go as low as 7-10%)
* **Wall Loops:** 2
* **Supports:** Normal supports with default settings (not tree supports)

Everything else was left as the default settings found in Bambu Studio.

Below are some details that summarizes all relevant details after slicing in Bambu Studio:

**Total Filament Usage (Including Supports):**

| Color | Filament Used|
|---|---|
| White | 18.76 g |
| Black | 35.00 g |
| Light Grey | 288.22 g |
| Transparent Red | 91.41 g |
| Transparent Blue | 31.82 g |
|  |  |
| **Total** | **465.20 g** |

**Costs:**

Regardless of actual filament, assume that all filament is acquired at the rate of $23/kg, which is similar to how much Bambu Lab PLA Basic filament costs. 

Total Cost = $0.023/g * 465.20 g = **$10.70**

**Time:** 

Total time spent printing is calculated at 13 hours 56 minutes (across 7 plates) according to Bambu Studio using default settings for speed.

### Assembly

Below are a few tables that show a list of components and hardware required:

| 3D Printed Part | Subsystem | Quantity |
|---|---|---|
| Camera Frame Corner Sleeve | Camera Mounting | 4 |
| Camera Frame | Camera Mounting | 1 |
| Top Plate | Camera Mounting | 1 |
| 12-14oz Coffee Cup | Sorting | 2 |
| Cup Base | Sorting | 2 |
| Cup 'Washer' | Sorting | 2 |
| Cup 'Drawer' | Sorting | 2 |
| Platform | Sorting | 1 |
| Ramp | Sorting | 1 |
| Servo Mount | Sorting | 1 |
| Platform | Sorting | 1 |
| Base | Body | 1 |
| Bottom | Body | 1 |
| Bin Label Plates | Body | 2 |
| LCD Screen Frame | Body | 1 |
| Shell | Body | 1 |

| Electrical Component | Quantity | Purpose |
|---|---|---|
| 1602 LCD Scren | 1 | Display key information and statistics to user |
| Green LED | 1 | Tells user object can be fed |
| Red LED | 1 | Tells user objects can NOT be fed |
| 10kΩ Potentiometer | 1 | Controls screen brightness |
| MicroServo 9G (SG90) | 1 | Rotate platform to move object for sorting into 'Target' or 'Not Target' bin |
| Walfront Camera Module | 1 | External USB Camera to provide view of object for YOLO to process |
| Arduino Leonardo | 1 | Communicates back and forth with Python app to perform key functions |
| Breadboard | 1 | Connects Arduino to External Power Source |
| Breadboard Power Supply Module + AC Adapter | 1 | Powers Servo, LCD Screen, and Arduino to take load off of Arduino and Laptop |
| M-M Breadboard Jumper Cables | Many | Creates electrical connection between components, power source, and Arduino pins without soldering |
| F-M Breadboard Jumper Cables | Many | Creates electrical connection between components, power source, and Arduino pins without soldering |

| Quantity x Screw Size | Purpose |
|---|---|
| 4 x M3 | Mounts Shell to Bottom; Threads + Nut Sticking out sits flush with base |
| 2 x M3 | Mounts LCD Screen Frame to Shell |
| 4 x M2 | Mounts 1602 LCD Screen to LCD Screen Frame |
| 2 x M3 | Mount Cup Washer + Cup Base + Cup 'Drawer' |
| 4 x M2 | Mount Bin Labels to Top of Shell |
| 6 x M2 <br/> 2 x M3 | Mount Ramp to Top of Shell (not all M2 screws needed; I used 2 x M3 and 2 x M2) |
| 2 x M3 | Mount Servo Mount to Top of Shell |
| 2 x M2 | Mount Servo to Servo Mount |
| 4 x M2 | Mount Camera Frame Corner Sleeve to Top of Shell |
| 4 x M2 | Mount Top Plate to Camera Frame |

**Quick Assembly Notes:**

1) **How to assemble platform to servo:** You will notice that the platform presses directly onto the splined shaft of the servo. The way I was able to achieve this was by using some accessories you get with servo motors. First, take any arm of the servo you were given (I elected to use the single arm piece given) and cut around the center female splined portion. After that, use some super glue and glue that small part into the side of the platform that has an opening for it (should fit snug). Wait for the glue to dry before assembly. To make a stronger bond, I would suggest using something like PLA Bond to increase the strength of the bond but that is not super necessary. I used the following video for inspiration, and you can use as a refernce should you want to recreate the assembly instructions: [Video](https://www.youtube.com/watch?v=zr02G2yCvGU).

2) The end of the Platform that has the shaft sticking out had to be sanded/filed down slightly in my case.

3) The holes on the LCD Screen Frame were originally intended to accomodate four M3 screws to hold the screen, but actually work better using four M2 screws.

4) The Camera does not slot in anywhere, but it is instead sandwiched between the Camera Frame and Top Plate to keep it held in place. 

**Pictures (electronics not wired and LEDs not installed):**

<div class="image-grid" markdown>

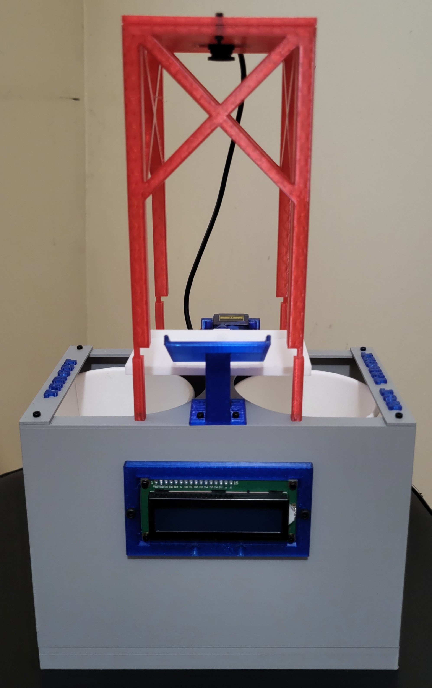
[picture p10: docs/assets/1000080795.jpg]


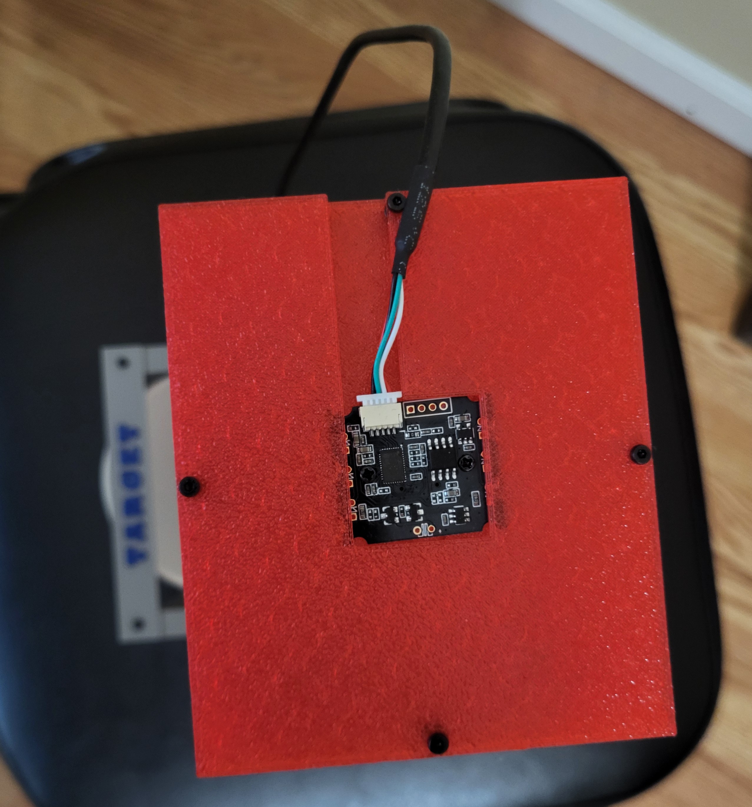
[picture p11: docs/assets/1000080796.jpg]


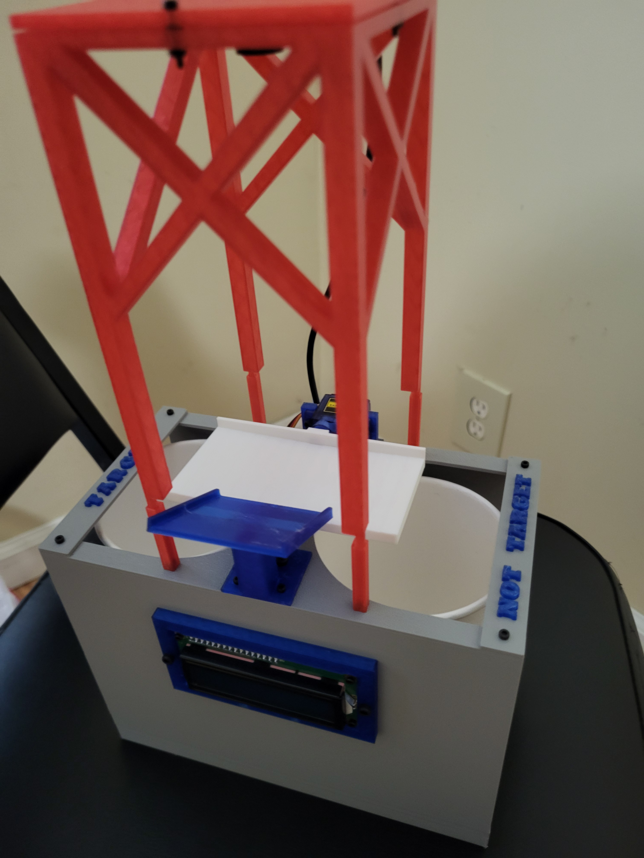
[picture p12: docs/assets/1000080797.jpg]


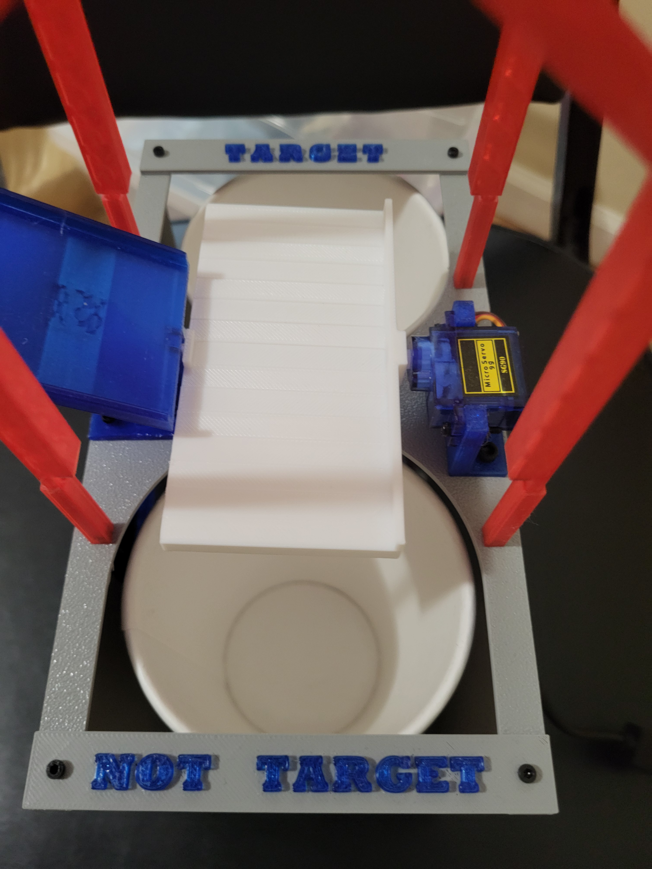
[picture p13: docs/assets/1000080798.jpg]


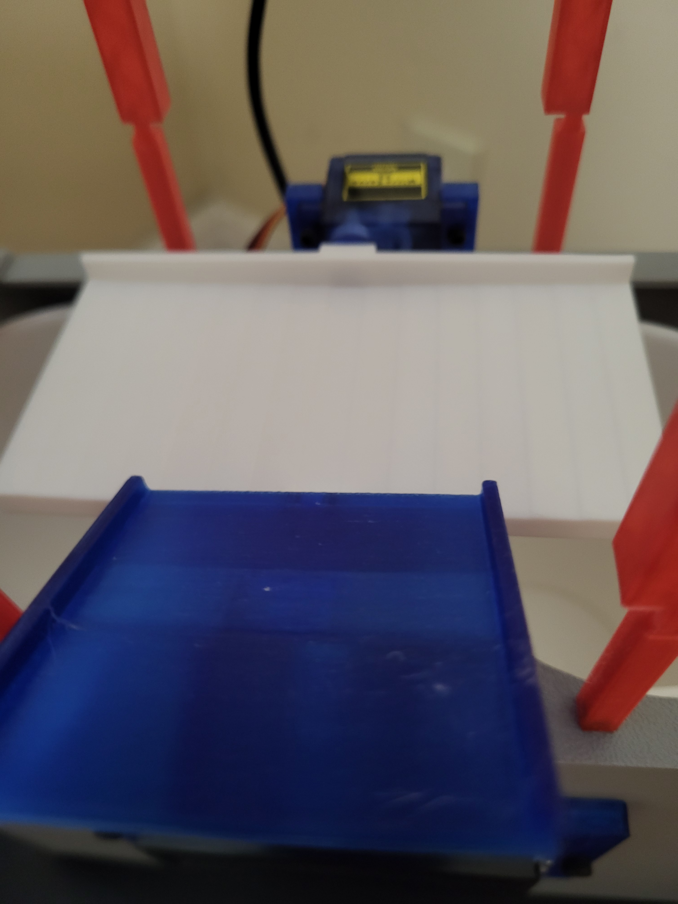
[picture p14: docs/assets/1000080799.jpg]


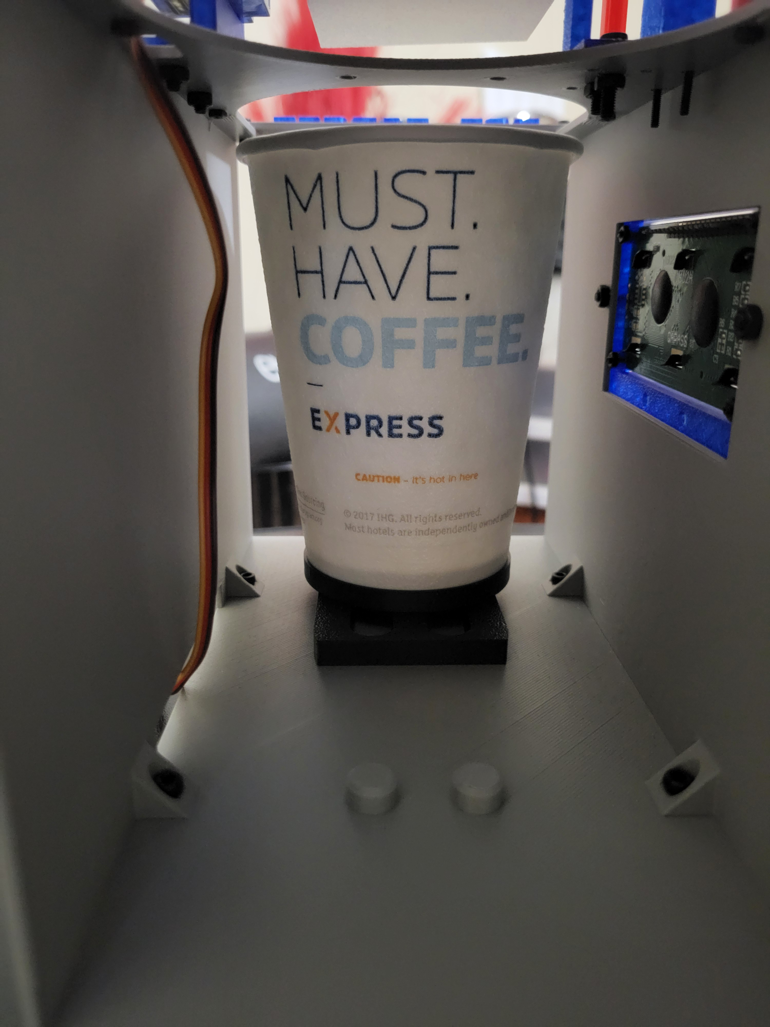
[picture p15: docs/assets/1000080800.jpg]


</div>

Feel free to print this out yourself! Use the .3mf if you have a slicing software that can run it, otherwise I have included the stl/step files needed. Note that the zip files will require you to manually add the names of the bins to the bin labels.

<div align="center">
  <a class="md-button md-button--primary" href="assets/YOLO Object Sorter Version 2.0.3mf" download>
    Download 3MF
  </a>
  <a class="md-button md-button--primary" href="assets/Object Sorter STL Files.zip" download>
    Download STL/STEP ZIP
  </a>
</div>

### Wiring

Below is a wiring diagram: 

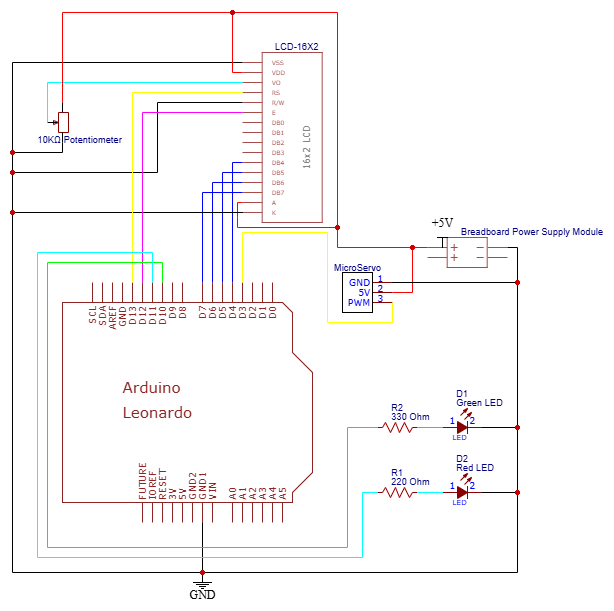
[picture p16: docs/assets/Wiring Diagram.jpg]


### Testing

Note that this section refers to testing beyond any fit checks and clearances between any hardware, holes, etc present while assembling the prototype. In other words, the prototype is FULLY assembled by this point and theoretically, if the Arduino code was inputted for the final product, then the system would run (i.e. no wiring changes, etc).

Before moving on to final integration, the prototype must be tested for a few things to see how it works. This is to ensure that a proof of concept for a strong path forward before working on a more advanced version of the software and integration. 

Here is a list of components and/or systems that MUST function properly to ensure that the full prototype works properly:

* Green LED
* Red LED
* 1602 LCD Screen
* Servo + Platform

The most effective way to test everything at once is to write some code that covers across all components. The code is included below, but first, here are some of the features of the code:

1. Green and Red LEDs are constantly blinking every couple seconds to ensure those are working properly.
2. LCD Screen displays a welcome message and displays the angle that the servo motor is at.
3. Servo and Platform rotation is tracked and can be calibrated so the correct servo angles can be inputted into the final code. Also, platform must be tested to ensure objects can actually fall into both cups for sorting, which is done manually now since the camera is not connected to YOLO.

Code below:

``` cpp title="electronics_testing.ino" linenums="1"
/*
 * Servo Position Tuner with LED & LCD - Arduino Leonardo
 * 
 * Hardware:
 * - Servo on pin 3
 * - Green LED on pin 10
 * - Red LED on pin 11
 * - LCD: RS=13, E=12, DB4=4, DB5=5, DB6=6, DB7=7
 * 
 * Commands:
 * - 0-180: Move to position
 * - 'h': Set HOME position
 * - 'l': Set LOW limit
 * - 'u': Set UPPER limit
 * - 's': Start sweep
 * - 'x': Stop sweep
 * - 'p': Print settings
 * - 'g': Go to HOME
 * - 'o': Go to LOWER LIMIT
 * - 'i': Go to UPPER LIMIT
 */

#include <Servo.h>
#include <LiquidCrystal.h>

// Pin definitions
const int servoPin = 3;
const int greenLED = 10;
const int redLED = 11;

// LCD: RS, E, D4, D5, D6, D7
LiquidCrystal lcd(13, 12, 4, 5, 6, 7);

Servo myServo;

// Position variables
int currentPos = 90;
int homePos = 90;
int lowLimit = 0;
int upperLimit = 180;

// Sweep variables
bool isSweeping = false;
int sweepDirection = 1;
int sweepSpeed = 15;

// LED timing
unsigned long lastLEDToggle = 0;
bool greenState = true;

// Display state
bool showingWelcome = true;

void setup() {
  Serial.begin(9600);
  
  // Setup LEDs
  pinMode(greenLED, OUTPUT);
  pinMode(redLED, OUTPUT);
  digitalWrite(greenLED, HIGH);
  digitalWrite(redLED, LOW);
  
  // Setup servo
  myServo.attach(servoPin);
  delay(100);
  myServo.write(currentPos);
  
  // Setup LCD
  lcd.begin(16, 2);
  delay(50);
  lcd.clear();
  lcd.setCursor(0, 0);
  lcd.print("  SERVO TUNER");
  lcd.setCursor(0, 1);
  lcd.print("  Welcome!");
  
  Serial.println("=== Servo Position Tuner ===");
  Serial.println("Commands:");
  Serial.println("  0-180: Move to position");
  Serial.println("  h: Set HOME position");
  Serial.println("  l: Set LOW limit");
  Serial.println("  u: Set UPPER limit");
  Serial.println("  s: Start sweep");
  Serial.println("  x: Stop sweep");
  Serial.println("  p: Print settings");
  Serial.println("  g: Go to HOME");
  Serial.println("  i: Go to UPPER limit");
  Serial.println("  o: Go to LOWER limit");
  Serial.println("===========================");
  printSettings();
}

void loop() {
  // Handle LED blinking (every 1 second)
  unsigned long currentMillis = millis();
  if (currentMillis - lastLEDToggle >= 1000) {
    lastLEDToggle = currentMillis;
    greenState = !greenState;
    
    if (greenState) {
      digitalWrite(greenLED, HIGH);
      digitalWrite(redLED, LOW);
    } else {
      digitalWrite(greenLED, LOW);
      digitalWrite(redLED, HIGH);
    }
  }
  
  // Handle sweeping
  if (isSweeping) {
    currentPos += sweepDirection;
    
    if (currentPos >= upperLimit) {
      currentPos = upperLimit;
      sweepDirection = -1;
    } else if (currentPos <= lowLimit) {
      currentPos = lowLimit;
      sweepDirection = 1;
    }
    
    myServo.write(currentPos);
    updateLCD();
    delay(sweepSpeed);
  }
  
  // Handle serial commands
  if (Serial.available() > 0) {
    String input = Serial.readStringUntil('\n');
    input.trim();
    
    if (input.length() == 0) return;
    
    // Switch from welcome to angle display on first command
    if (showingWelcome) {
      showingWelcome = false;
      updateLCD();
    }
    
    char cmd = input.charAt(0);
    
    // Check if it's a number
    if (isDigit(cmd)) {
      int pos = input.toInt();
      if (pos >= 0 && pos <= 180) {
        isSweeping = false;
        currentPos = pos;
        myServo.write(currentPos);
        updateLCD();
        Serial.print("Moved to position: ");
        Serial.println(currentPos);
      } else {
        Serial.println("Position must be 0-180");
      }
    }
    // Handle letter commands
    else {
      switch (cmd) {
        case 'h':
        case 'H':
          homePos = currentPos;
          Serial.print("HOME set to: ");
          Serial.println(homePos);
          break;
          
        case 'l':
        case 'L':
          lowLimit = currentPos;
          Serial.print("LOW limit set to: ");
          Serial.println(lowLimit);
          break;
          
        case 'u':
        case 'U':
          upperLimit = currentPos;
          Serial.print("UPPER limit set to: ");
          Serial.println(upperLimit);
          break;
          
        case 's':
        case 'S':
          isSweeping = true;
          sweepDirection = 1;
          Serial.println("Sweeping started");
          break;
          
        case 'x':
        case 'X':
          isSweeping = false;
          Serial.println("Sweeping stopped");
          break;
          
        case 'p':
        case 'P':
          printSettings();
          break;
          
        case 'g':
        case 'G':
          isSweeping = false;
          currentPos = homePos;
          myServo.write(currentPos);
          updateLCD();
          Serial.print("Moved to HOME: ");
          Serial.println(homePos);
          break;
          
        case 'i':
        case 'I':
          isSweeping = false;
          currentPos = upperLimit;
          myServo.write(currentPos);
          updateLCD();
          Serial.print("Moved to UPPER limit: ");
          Serial.println(upperLimit);
          break;
          
        case 'o':
        case 'O':
          isSweeping = false;
          currentPos = lowLimit;
          myServo.write(currentPos);
          updateLCD();
          Serial.print("Moved to LOWER limit: ");
          Serial.println(lowLimit);
          break;
          
        default:
          Serial.println("Unknown command");
      }
    }
  }
}

void updateLCD() {
  lcd.clear();
  lcd.setCursor(0, 0);
  lcd.print("SERVO ANGLE:");
  lcd.setCursor(0, 1);
  lcd.print(currentPos);
}

void printSettings() {
  Serial.println("\n--- Current Settings ---");
  Serial.print("Current Position: ");
  Serial.println(currentPos);
  Serial.print("HOME Position: ");
  Serial.println(homePos);
  Serial.print("LOW Limit: ");
  Serial.println(lowLimit);
  Serial.print("UPPER Limit: ");
  Serial.println(upperLimit);
  Serial.print("Sweeping: ");
  Serial.println(isSweeping ? "YES" : "NO");
  Serial.println("------------------------\n");
}
```

Below is some images and a video of how the electronics test was assembled. Note that it was not assembled on the actual prototype for two reasons:

1) To make sure the concept actually works before fully assembling it and wiring it together.

2) At the time of testing, I didn't have the necessary jumper cables to do a proof of concept test on the actual prototype. This meant that I couldn't assemble it on the actual product just yet, but I was able to test all electronics to see if it was working.

It is also important to note that some may experience difficulties with assembly and/or testing. There are generally two types of issues, one of which is software issues, and the other of which is hardware issues. Common software issues usually fall under either a code that has bugs or code that has faulty logic, both of which can still occur despite using AI tools for coding. Common hardware issues include the following: damaged Arduino pins, faulty chip on the Arduino, loose connections, faulty wires, faulty wiring, faulty breadboard, etc. The only major problem I had with the wiring was actually a faulty breadboard, which meant I had to rewire the entire circuit on a different breadboard. 

<div class="image-grid" markdown>

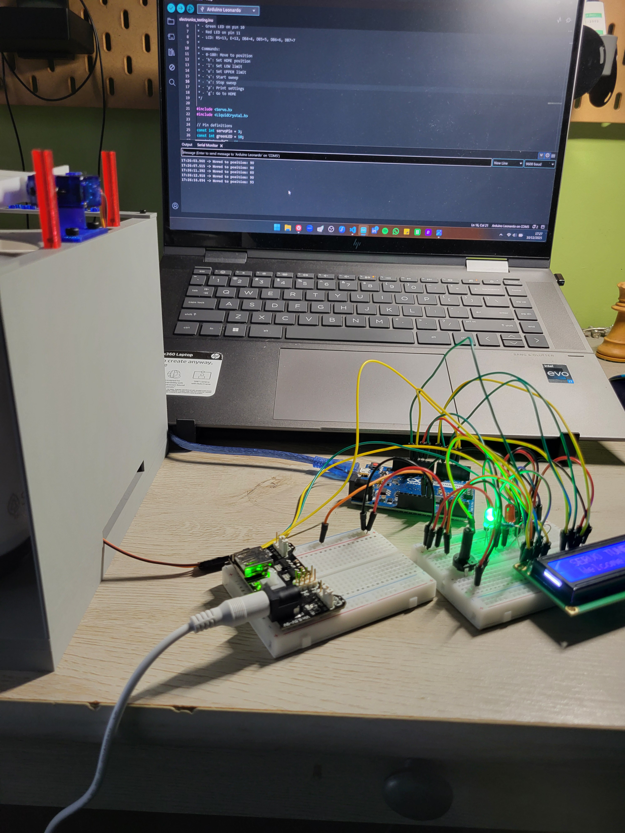
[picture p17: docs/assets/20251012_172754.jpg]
Prototype 1


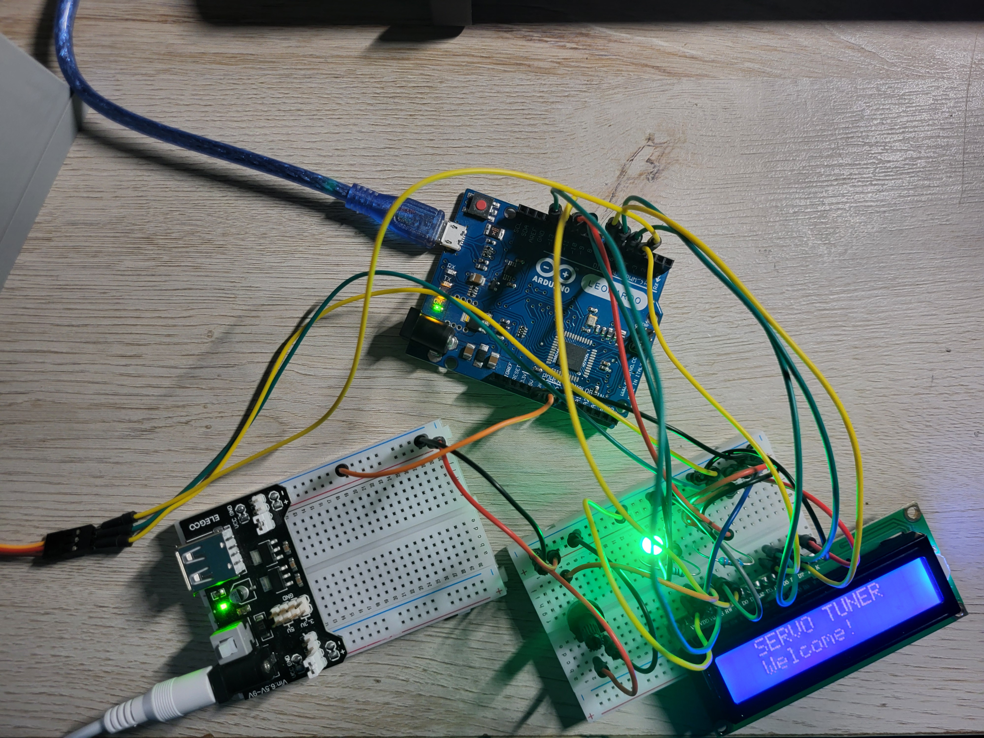
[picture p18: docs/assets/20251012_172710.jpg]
Prototype 2


</div>

<div class="video-wrapper">
  <iframe 
    src="https://www.youtube.com/embed/MREHpypb1wQ?mute=1&rel=0&playsinline=1"
    title="Test Setup"
    frameborder="0"
    allow="autoplay; encrypted-media"
    allowfullscreen>
  </iframe>
</div>

<div class="video-caption" align="center">
  <em>Video showing electronics and wiring</em>
</div>

<div><br></div>

The way I approached testing was to show a proof of concept for all working systems, including mechanical and electrical. The code above was able to get the electronics working, which entailed getting the platform rotated. However, the prototype will only have a good proof of concept if it can theoretically send objects to any bin while also relaying information on the screen. Something important to note is that I am manually telling the servo to move to a certain angle, whereas in the final testing, it will be automated based on the objects fed, the user demands, and of course, the pytorch model loaded.

Therefore, I decided to put it to the test by sending a small sample set of objects. Below are the exact objects I used while testing, and a ruler to give an idea of the general size of these objects:

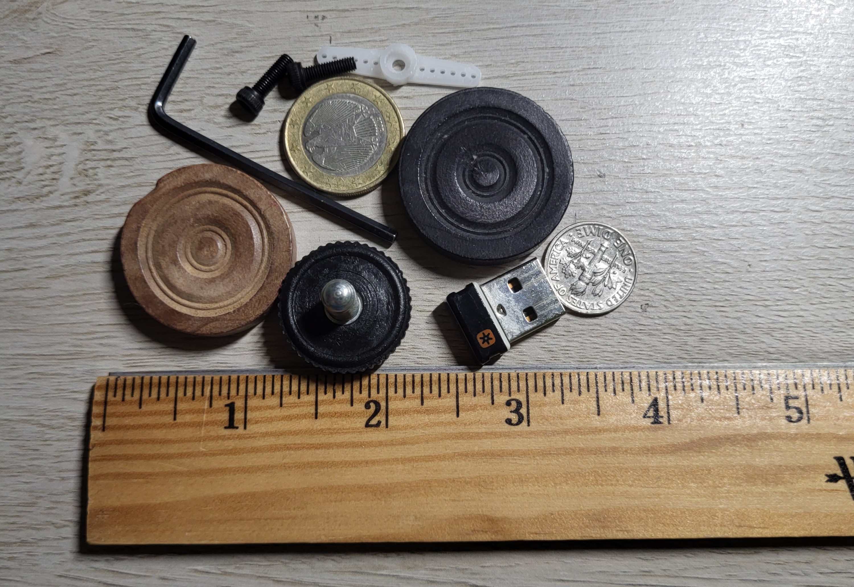
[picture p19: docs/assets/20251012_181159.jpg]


And now, the test video below:

<div class="video-wrapper">
  <iframe 
    src="https://www.youtube.com/embed/3prBVpu9qB8?mute=1&rel=0&playsinline=1"
    title="Prototype Testing"
    frameborder="0"
    allow="autoplay; encrypted-media"
    allowfullscreen>
  </iframe>
</div>

<div class="video-caption" align="center">
  <em>Video depicting test being carried out</em>
</div>

<div><br></div>

Testing Observations:

* Using the code above, I figured out that the upper limit was 135 degrees and the lower limit was 55 degrees, which gives a sweeping motion of 80 degrees, or about 40 degrees on each side. This was more than I had expected from when I was modelling the prototype in CAD. The final tuning will be done before final testing if needed.
* All the electronics work as expected. The screen turns on, gives a welcome message, and relays the servo angles at all times when there is a change. The LCD also works as expected, and the potentiometer does, in fact, adjust the brightness as required. The LEDs alternate turning on and off while power is being given. The servo also turns as expected, which a relatively quick response time to any inputs.

### Conclusion 

With all the success of the assembly and testing, I think this is a solid prototype to move forward with the project. 

Any changes that have to be made to the prototype are all considered minor, and will be documented and finalized in the integration stage.

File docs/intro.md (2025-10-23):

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

An ideal device would be able to use an image of the product, identify what it is, and sort it based on the context of what would be coming into the device. This type of device can be designed using machine learning (ML), which is trained using images of a certain category. Note that this is a simplified version of the pipeline, and a more detailed pipeline will be ironed out in later phases of the design and prototyping process. There are various pros and cons to using ML in such an application, with the biggest pro being the ability to make an inefficient process more efficient and the biggest con being that the ability of the device functioning properly depends entirely on how well the ML implementation is done. 

To my knowledge, there is not such a device in the market, but there are aspects of the solution that are working in the market, and serve as a proof of concept. The first of these are a series of apps that are able to use the image of a coin to be able to give relevant information to the user. An example of such an app is “CoinSnap”, which allows users to scan coins and be provided with information and facts about that specific coin. This idea can be extended to similar apps on a smartphone for different purposes, such as identifying stars in the night sky or even forms of wildlife. 

A second working proof of concept serves as a working example of such a device. A company called Bulher has created a sorting device that can sort things such as agricultural seeds, coffee beans, etc in their “SORTEX” lineup. The device uses an optical sensor to be able to sort out a sample given the respective categories. 

But what if there was a solution that was more modular, something that could plug into a laptop and leverage its webcam to be able to physically sort through objects, not just identify them?

<div><br></div>

**_References:_**

Market Research:

* [Want to “change” your fortune? Coin apps might help](https://www.fourstateshomepage.com/news/local/do-you-want-to-change-your-fortune-coin-apps-might-help/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,coins%2C%20and%20most%20users%20agree.) &rarr; Apps that take image of coins and are able to figure out its value

* [GitHub - thim0o/CoinDetector](https://github.com/thim0o/CoinDetector) &rarr; An image based coin counter using Python and Tensorflow
Coin Detector on GitHub

* [Optical Sorting Machines](https://www.buhlergroup.com/global/en/process-technologies/Optical-Sorting.html) &rarr; Working Concept within Agriculture

Publications:

* [Cell.com |  Intelligent Image-Activated Cell Sorting](https://www.cell.com/cell/pdf/S0092-8674(18)31044-4.pdf)
* [Nanocellect | Image-guided cell sorting technical overview](https://nanocellect.com/image-guided-cell-sorting/)

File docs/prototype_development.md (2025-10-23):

This page provides a little introduction to what is required by the prototype and how I aim to solve those requirements. 

## Requirements

First off, here is a list of basic requirements:

* Prototype must allow user to be able to load objects with relative ease, without having to worry too much about the orientation and the type of object loaded.
* Prototype must be able to work with, or show potential to work with, a variety of objects with differing geometry, weight, size, etc.
* Prototype must allow objects to be visible from the webcam and allow the YOLO software to be able to detect and sort objects.
* Prototype must accomodate a "target" and "other" bin, to allow for binary sorting.
* Prototype must allow all electronics to be easily accessible to user to allow for debugging and/or allow for any required work to be performed (rewiring, reconnecting, etc) while also not interfering with the sorting process.
* Prototype must contain a manual override to allow for human intervention in case of failure or unexpected errors.
* Prototype must be able to sort, or show potential to sort, with relative high accuracy.

<div><br></div>

**The list above details all basic requirements, however it leaves out a few desireable features, which would be implemented if the project timeline were to be extended. Ideally, the prototype will also contain:**

* **Error Handling &rarr;** System should have a way of knowing when something has gone wrong and attempt a correction.
* **Scalability &rarr;** System should be "plug and play", where there would not be much work to scale this up to whatever application it is required for.

<div><br></div>

## Final Prototype Solution (Ver 2.X -- 9/30/25)

After speaking with my project mentor, we came to the conclusion that the solution decided on in Version 1.X (Vibration Bowl Feeder + Conveyor Belt) is not ideal for the scope of the project. Pursuing that route would add a lot of complexities with regards to the object feeding, which is not super in line with the scope of the project. While an automated system to feed objects pretty much effortlessly is a solid idea, it is indeed out of scope. 

The main focus of the project is on object detection and using various models to be able to detect and sort objects. That being said, object feeding will be done manually and is not a part of the project I will be designing too much.

Here is the path forward with regards to the prototype: 

1. Use an external webcam to allow for greater flexibility. 
2. Create a standalone device that is not attached to the computer in any way (minus any external webcam connections via USB), so that any changes in laptop size and type can be negated and produce something more universal.

I am providing a brief concept sketch below to detail what the standalone device might look like: 

Concept Sketch for Version 2.X

Below I am doing a requirements check on the object feeding and object transportation, comparing the idea of a standalone device against the selected solutions from Version 1.X. 

### Object Feeding

What is being compared?

* Vibration Bowl Feeder
* Manual feeding into standalone device

| Requirement | Vibration Bowl Feeder | Manual Feeding | Notes / Explanation|
|---|---|---|---|
| Easy loading of objects without worrying about orientation or type | ✔️ Meets | ✔️ Meets | Vibration Bowl Feeders can feedmore consistently and reliably (IF designed correctly); Manual Feeding is simpler and orientation can be controlled by user |
| Works with a variety of object sizes, weights, and shapes | ⚠️ Partially meets | ✔️ Meets | Viration Bowl Feeder is limited by the bowl geometry, but manual feeding can work with objects of any geometry (as long as the chute/ramp to feed is large enough) |
| Allows objects to be visible for YOLO detection | ➖ No effect | ➖ No effect | Object visibility depends on camera setup, independent of method of feeding |
| Accommodates “target” and “other” sorting bins | ➖ No effect | ➖ No effect | Sorting bins are outside the feeder design |
| Electronics easily accessible for debugging | ➖ No effect | ➖ No effect | Electronics housing will be designed separately |
| Manual override for human intervention | ➖ No effect | ➖ No effect | Manual override controlled elsewhere, not part of feeder |
| High accuracy sorting capability | ➖ No effect | ➖ No effect | Sorting accuracy depends on YOLO models |

Even from the table above, the manual feeding is simpler due to less complexity with mechanical components, and more importantly, vibrations. Designing for vibrations is inherently difficult, and even if the feeder was designed and could feed objects up, there will always be a type of object ill-suited to be fed down to either geometry or object's natural frequency. 

### Transporting Objects for Detection and Sorting

While a comparison can be drawn for the transportation of objects, something of note is that there are two totally different ideas in play. 

Version 1.X had the idea of taking objects and having be fed out and moved into view, however, as specified in the concept sketch for Version 2.X, objects will be fed by means of a gravity hopper or manual feeding directly into the view of the object. This induces much less mechanical complexity as a whole and thus there is a very clear, straightforward, and obvious path forward. 

### Comparison of Overall Concepts

Below is a brief description of both concepts. Note that it includes the object's point of view as it travels to the bins.

* Version 1.X: Vibration Bowl Feeder &rarr; 3D Printed Conveyor Belt &rarr; Webcam's FOV (viewable by using mirror to reorient FOV) &rarr; Bins
* Version 2.X: Manual Feeding (via hopper/ramp/chute) &rarr; Platform (within Webcam's FOV) &rarr; Bins

I will do two comparisons, one against the requirements as a whole and one that details prototype feasibilty relative to one another.

| Requirement | Version 1.X | Version 2.X | Notes / Explanation|
|---|---|---|---|
| Easy loading of objects without worrying about orientation or type | ✔️ Meets, but with correct, finely tuned design | ✔️ Meets, but more user effort |  |
| Works with a variety of object sizes, weights, and shapes | ⚠️ Partially meets | ✔️ Meets | Version 1.X is limited by bowl geometry, while Version 2.X can work with a greater variety of objects |
| Allows objects to be visible for YOLO detection | ✔️ Meets | ✔️ Meets | Both concepts leverage a camera to be able to view and detect objects |
| Accommodates “target” and “other” sorting bins | ✔️ Meets | ✔️ Meets | Both accomodate bins to be able to sort objects |
| Electronics easily accessible for debugging | ✔️ Meets | ✔️ Meets | Electronics will be housed separately in both cases, but can be made easily accessible  |
| Manual override for human intervention | ✔️ Meets | ✔️ Meets | Manual override can be built in |
| High accuracy sorting capability | ✔️ Meets | ✔️ Meets | Sorting accuracy depends on YOLO models, which is able to be leveraged in both cases |

| Prototype Feasibility Requirement | Version 1.X | Version 2.X | Notes / Explanation|
|---|---|---|---|
| Relative Mechanical Complexity | 🔴 More complex| 🟢 Less complex | |
| Relative Electrical Complexity | 🔴 More complex | 🟢 Less complex | Version 1.X will need a vibration motor and a DC motor to move the belt, Version 2.X will need a servo motor to control the platform |
| Relative Costs | 🔴 More | 🟢 Less | Both will cost a similar amount to put together, which includes costs of making and sourcing components|
| Prototype-able? | 🔴 Less prototype-able | 🟢 More prototype-able | Both concepts can be 3D printed and integrated, but Version 1.X requires more components that have to be carefully designed with vibrations in mind|
| Reproducible? | 🔴 Not really | 🟢 Yes, easily | Reasoning due to ability to prototype |
| Scalable | 🔴 Less scalable | 🟢 More scalable | Version 2.X is simpler, and will be easier to assemble and modify for larger sized objects |

## Considered Solutions (Ver 1.X -- 8/26/25)

**NOTE:** This is an older version of the prototype that is not being considered after 8/26/25. I have retained the information below for documentation and reference purposes.

Based on the list of basic requirements above, here are solutions being considered for the broader aspects of the prototype.

### Object Feeding

What is being considered?

* Vibration Bowl Feeder
* Centrifugal Feeder

| Requirement | Vibration Bowl Feeder | Centrifugal Feeder | Notes / Explanation|
|---|---|---|---|
| Easy loading of objects without worrying about orientation or type | ✔️ Meets | ✔️ Meets | Vibration Bowl Feeders feed slower, but are more reliable; Centrifugal will require a stronger motor or a high torque gear train, is simpler, but is less universal |
| Works with a variety of object sizes, weights, and shapes | ⚠️ Partially meets | ⚠️ Partially meets | Both concepts are limited by bowl geometry to an extent, but not heavily affected by it for prototype purposes |
| Allows objects to be visible for YOLO detection | ➖ No effect | ➖ No effect | Object visibility depends on camera setup, independent of feeder |
| Accommodates “target” and “other” sorting bins | ➖ No effect | ➖ No effect | Sorting bins are outside the feeder design |
| Electronics easily accessible for debugging | ➖ No effect | ➖ No effect | Electronics housing will be designed separately |
| Manual override for human intervention | ➖ No effect | ➖ No effect | Manual override controlled elsewhere, not part of feeder |
| High accuracy sorting capability | ➖ No effect | ➖ No effect | Sorting accuracy depends on YOLO models |

When comparing both solutions on paper, there is no obvious standout choice to start with, I will also do a quick comparison below to highlight a path forward.

| Prototype Feasibility Requirement | Vibration Bowl Feeder | Centrifugal Feeder | Notes / Explanation|
|---|---|---|---|
| Relative Mechanical Complexity | 🟢 Less complex | 🔴 More complex | Vibration Bowl Feeder will have less mechanical components to work with; Centrigufal Feeder will have more mechanical components to work with and has to be designed more carefully|
| Relative Electrical Complexity | 🔴 Slightly more complex | 🟢 Slightly less complex | Vibration Bowl Feeders will need extra tuning and sourcing of electrical components; Centrifugal Bowl Feeders will require less elctrical components and thus less complexity |
| Relative Costs | ⚪ Similar | ⚪ Similar | Both will cost a similar amount to put together, which includes costs of making and sourcing components|
| Prototype-able? | ⚪ Similar | ⚪ Similar | Both concepts can be 3D printed |
| Reproducible? | 🟢 Slightly More | 🔴 Slightly Less | Vibration Bowl Feeders have less parts to put together, which reduces chances of parts not fitting together after 3D printing |
| Scalable | ⚪ Similar | ⚪ Similar | Both concepts can be adapted and scaled in a post-project timeline to fit the needs required through changing out any components that were sourced and altering dimensions in CAD |

Both are pretty equal in terms of viablility, but the vibration bowl feeder is slightly less complex overall and has the potential to be more reproducible to other people. Therefore, I will stick to making a vibration bowl feeder for now.

### Transporting Objects for Detection and Sorting

This section deals with solutions being considered to handle moving the objects being sorted from the feeding mechanism to the webcam'e field of view and then to the bins. 

What is being considered?

* **Option 1:** System of Linear Tracks &rarr; Webcam's FOV (via a enclosure) &rarr; Bins
* **Option 2:** 3D Printed Conveyor Belt &rarr; Webcam's FOV (viewable by using mirror to reorient FOV) &rarr; Bins

| Requirement | Option 1 | Option 2 | Notes / Explanation|
|---|---|---|---|
| Easy loading of objects without worrying about orientation or type | ⚠️ Potential negative | ✔️ Meets |  I will focus on loading in the context of going to webcam FOV and then to bins; Option 1 has to be designed carefully to accomodate a vast amount of objects; Option 2 is more universal and doesn't deoend on orientation or type |
| Works with a variety of object sizes, weights, and shapes | ⚠️ Potential Negative | ✔️ Meets | Option 1 is limited in terms of track geometry; Option 2 more universal |
| Allows objects to be visible for YOLO detection | ⚠️ Potential Negative | ✔️ Meets | Option 1's enclosure has to designed to either allow in natural ambient light or be well-lit; Option 2 uses ambient lighting, which works reasonably well |
| Accommodates “target” and “other” sorting bins | ✔️ Meets | ✔️ Meets | Sorting bins can be integrated into both solutions |
| Electronics easily accessible for debugging | ➖ No effect | ➖ No effect | Electronics housing will be designed separately |
| Manual override for human intervention | ➖ No effect | ➖ No effect | Manual override controlled elsewhere, not part transportation sub-system |
| High accuracy sorting capability | ➖ No effect | ➖ No effect | Sorting accuracy depends on YOLO models |

Based on requirements alone, there is a clear path forward. At worst, a conveyor belt will be able to provide more proof of concept than the linear track system, and at best, it will be a sub-system that is more universal. No feasibility study will be conducted unless something goes wrong with the conveyor belt concept.

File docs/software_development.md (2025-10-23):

This section of the website is dedicated to getting a minimum viable software developed, before truly getting it integrated in context to the whole system. The software was developed before any physical prototype was designed or assembled. 

View the progression through the software development via the collapsible menu on the left.

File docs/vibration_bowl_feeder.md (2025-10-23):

The focus for development will first be on the vibration bowl feeder, as that is the more difficult thing to prototype between the vibration bowl feeder and the conveyor belt system. 

## Version 1.1 (Bowl Feeder)

A design relatively similar to those found in industry and automation will try to be emulated, as it has strong proof of concept. Below is a list of either designed or sourced components to build the bowl feeder:

* Bowl
* 3x 1027 Vibration Motors
* Underside Bowl Motor Holder (to ensure motors are pressed against bowl to transfer vibrations)
* 3x Shims set 120 degrees apart (to add dampening to system)
* Hardware

<div><br></div>

### CAD

Pictures of Components and Assembly (Click thumbnail to enlarge):

<!-- Lightbox overlay -->
<div id="lightbox" style="display:none; position:fixed; top:0; left:0; width:100%; height:100%;
  background: rgba(0,0,0,0.8); justify-content:center; align-items:center; z-index:1000;">
  <button id="prevBtn" style="position:absolute; left:20px; color:white; font-size:2rem; background:none; border:none; cursor:pointer;">&#10094;</button>
  
  <button id="nextBtn" style="position:absolute; right:20px; color:white; font-size:2rem; background:none; border:none; cursor:pointer;">&#10095;</button>
</div>

<style>
  #gallery img.thumb, #gallery2 img.thumb {
    width: 100%;
    height: auto;
    max-width: 200px;
    min-width: 150px;
    cursor: pointer;
    border-radius: 6px;
    transition: transform 0.2s;
    object-fit: cover;
    aspect-ratio: 4/3;
  }

  #gallery img.thumb:hover, #gallery2 img.thumb:hover {
    transform: scale(1.05);
  }

  @media (max-width: 600px) {
    #gallery img.thumb, #gallery2 img.thumb {
      max-width: calc(50% - 5px);
    }
  }

  #prevBtn, #nextBtn, #prevBtn2, #nextBtn2 {
    user-select: none;
  }
</style>

<script>
document.addEventListener("DOMContentLoaded", () => {
    const galleryDiv = document.getElementById('gallery');
    const lightbox = document.getElementById('lightbox');
    const lightboxImg = document.getElementById('lightbox-img');
    const prevBtn = document.getElementById('prevBtn');
    const nextBtn = document.getElementById('nextBtn');

    const images = [
    "../assets/1.1_Bowl.png",
    "../assets/1.1_Underside_1.png",
    "../assets/1.1_Underside_2.png",
    "../assets/1.1_Shim.png", 
    "../assets/1.1_Base.png",
    "../assets/1.1_Full_1.png",
    "../assets/1.1_Full_2.png",
    "../assets/1.1_Full_3.png",
    "../assets/1.1_Full_4.png",
    ];

    let currentIndex = 0;

    // Load thumbnails
    images.forEach((src, i) => {
    const thumb = document.createElement('img');
    thumb.src = src;
    thumb.className = 'thumb';

    thumb.onclick = () => openLightbox(i);

    galleryDiv.appendChild(thumb);
    });

    function openLightbox(index) {
    currentIndex = index;
    lightbox.style.display = "flex";
    lightboxImg.src = images[currentIndex];
    }

    function closeLightbox() {
    lightbox.style.display = "none";
    }

    function showNext() {
    currentIndex = (currentIndex + 1) % images.length;
    lightboxImg.src = images[currentIndex];
    }

    function showPrev() {
    currentIndex = (currentIndex - 1 + images.length) % images.length;
    lightboxImg.src = images[currentIndex];
    }

    // Navigation
    nextBtn.onclick = (e) => { e.stopPropagation(); showNext(); };
    prevBtn.onclick = (e) => { e.stopPropagation(); showPrev(); };

    // Close on background click
    lightbox.onclick = closeLightbox;

    // Keyboard controls
    document.addEventListener('keydown', (e) => {
    if (lightbox.style.display === "flex") {
        if (e.key === "ArrowRight") showNext();
        if (e.key === "ArrowLeft") showPrev();
        if (e.key === "Escape") closeLightbox();
    }
    });
 });
</script>

<div><br></div>

### Testing

No images/videos are present after the very brief testing session I had with Version 1.1. Below I have written out some observations of the test.

Observations:

* Prototype was easy to assembly (minus any soldering that had to be done due to the tiny wires and my inexperience)
* Despite using 3 1027 vibration motors, the objects did not move at all.
* The vibration power was way too low to be able to get the objects to vibrate. This was after testing various kinds of objects with various weights.

Conclusions:

* I severly underestimated the power of a 1027 vibration motor. They are best used to give haptic feedback, but not great for vibrating an entired bowl and any components within.
* This development path *might* have some scope, but is yet to be seen.

Path Forward:

* Source a stronger vibration motor that can also work with higher voltages.
* Adjust design to be able to accomodate new motor in such a way to add some dampening to ensure the right parts are vibrating. 

## Version 1.2 (Bowl Feeder)

This design is iterated on from Version 1.1, instead focusing on using a stronger vibration motor to be able to hopefully send objects up the correct path. 

Only major changes from this version and last are as follows:

a. Stronger motor to be used for this version, similar to [this](https://www.amazon.com/BOJACK-Vibration-Powerful-Electric-Vibrating/dp/B09XDWPMHY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) one from Amazon. 

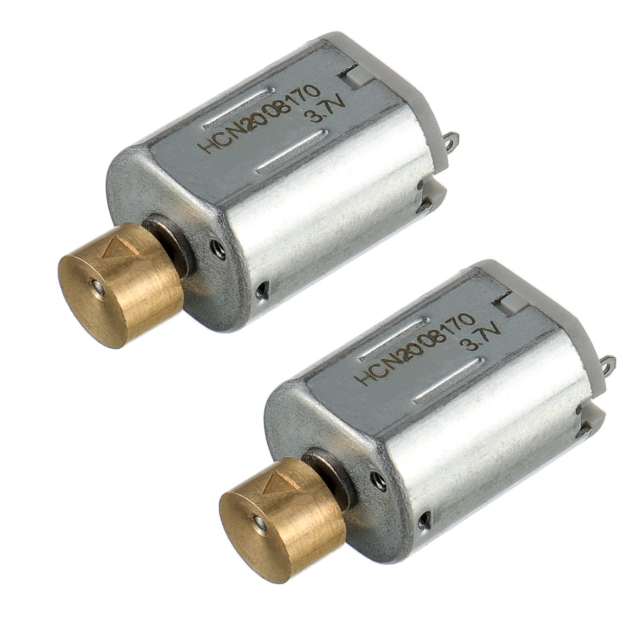
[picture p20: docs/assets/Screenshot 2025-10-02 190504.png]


b. Any related design changes made to be able to accomodate motors, which meant a redesign of the underside area of the bowl itself. 

List of components included in this design below:

* Bowl (same as before)
* Eccentric Rotating Mass Vibration Motor
* Motor Grip
* Motor Housing
* 3x Shims set 120 degrees apart (same as before)
* Hardware

### CAD

Pictures of Components and Assembly (Click thumbnail to enlarge):

<!-- Lightbox overlay -->
<div id="lightbox2" style="display:none; position:fixed; top:0; left:0; width:100%; height:100%;
  background: rgba(0,0,0,0.8); justify-content:center; align-items:center; z-index:1000;">
  <button id="prevBtn2" style="position:absolute; left:20px; color:white; font-size:2rem; background:none; border:none; cursor:pointer;">&#10094;</button>
  
  <button id="nextBtn2" style="position:absolute; right:20px; color:white; font-size:2rem; background:none; border:none; cursor:pointer;">&#10095;</button>
</div>

<script>
document.addEventListener("DOMContentLoaded", () => {
    const galleryDiv = document.getElementById('gallery2');
    const lightbox = document.getElementById('lightbox2');
    const lightboxImg = document.getElementById('lightbox-img2');
    const prevBtn = document.getElementById('prevBtn2');
    const nextBtn = document.getElementById('nextBtn2');

    const images = [
    "../assets/1.1_Bowl.png",
    "../assets/1.2_Underside_1.png",
    "../assets/1.2_Underside_2.png",
    "../assets/1.2_Grip_1.png",
    "../assets/1.2_Grip_2.png",
    "../assets/1.2_Grip_3.png",
    "../assets/1.2_Holder_1.png",
    "../assets/1.2_Holder_2.png",
    "../assets/1.2_Lid_1.png",
    "../assets/1.2_Lid_2.png",
    "../assets/1.1_Shim.png", 
    "../assets/1.2_Bottom_1.png",
    "../assets/1.2_Full_1.png",
    "../assets/1.2_Full_2.png",
    "../assets/1.2_Full_3.png",
    "../assets/1.2_Full_4.png",
    ];

    let currentIndex = 0;

    // Load thumbnails
    images.forEach((src, i) => {
    const thumb = document.createElement('img');
    thumb.src = src;
    thumb.className = 'thumb';

    thumb.onclick = () => openLightbox(i);

    galleryDiv.appendChild(thumb);
    });

    function openLightbox(index) {
    currentIndex = index;
    lightbox.style.display = "flex";
    lightboxImg.src = images[currentIndex];
    }

    function closeLightbox() {
    lightbox.style.display = "none";
    }

    function showNext() {
    currentIndex = (currentIndex + 1) % images.length;
    lightboxImg.src = images[currentIndex];
    }

    function showPrev() {
    currentIndex = (currentIndex - 1 + images.length) % images.length;
    lightboxImg.src = images[currentIndex];
    }

    // Navigation
    nextBtn.onclick = (e) => { e.stopPropagation(); showNext(); };
    prevBtn.onclick = (e) => { e.stopPropagation(); showPrev(); };

    // Close on background click
    lightbox.onclick = closeLightbox;

    // Keyboard controls
    document.addEventListener('keydown', (e) => {
    if (lightbox.style.display === "flex") {
        if (e.key === "ArrowRight") showNext();
        if (e.key === "ArrowLeft") showPrev();
        if (e.key === "Escape") closeLightbox();
    }
    });
});
</script>

<div><br></div>

### Testing

A few images are included below to show the final result of the assembly, along with my obvervations for the test.

<div style="display: grid; grid-template-columns: repeat(auto-fit, minmax(250px, 1fr)); gap: 10px; max-width: 800px;">
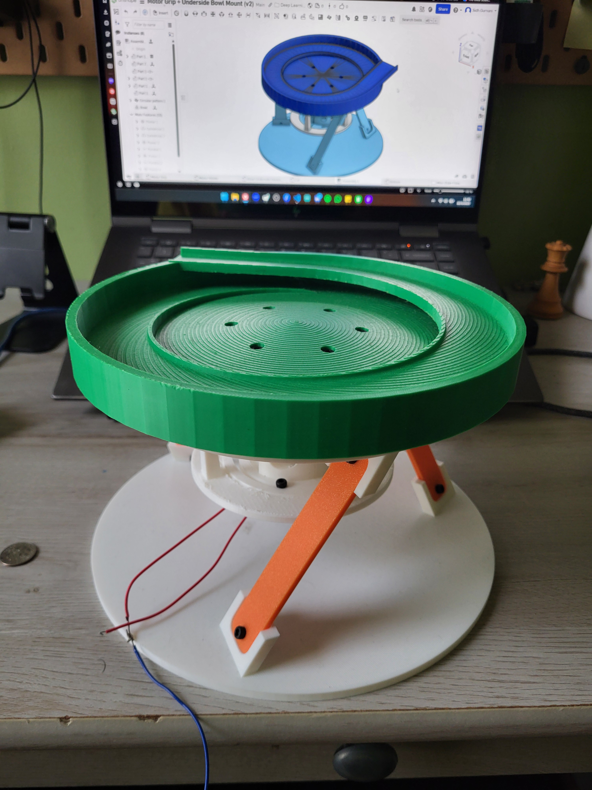
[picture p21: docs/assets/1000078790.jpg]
  
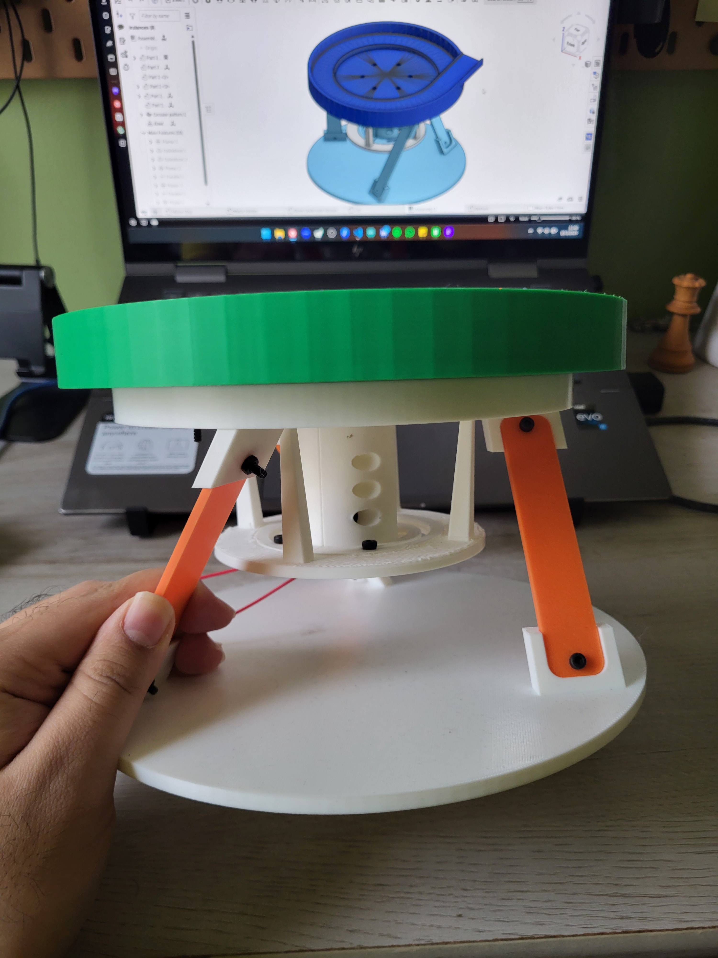
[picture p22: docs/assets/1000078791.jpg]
  
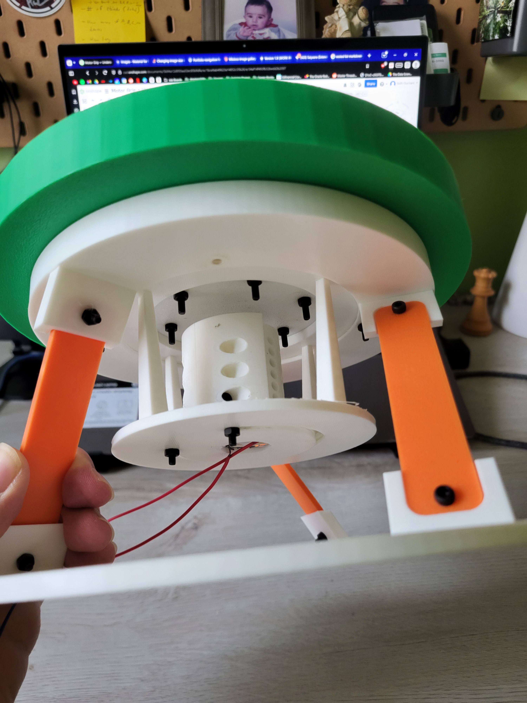
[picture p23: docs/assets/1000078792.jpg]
  
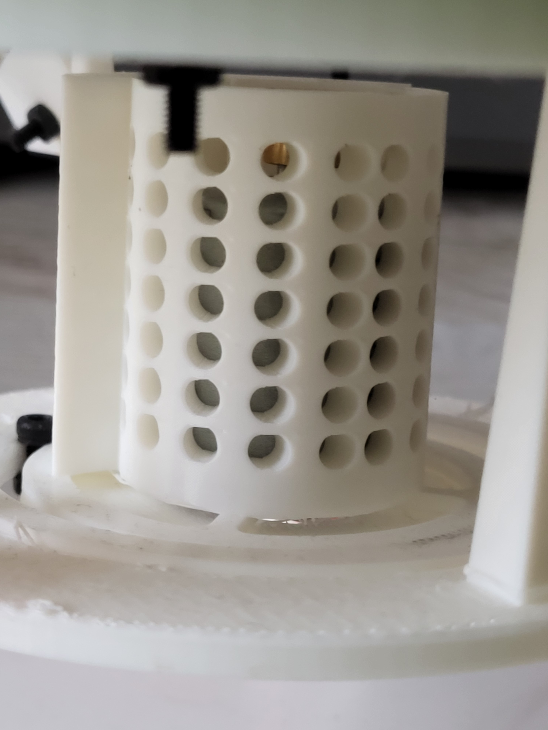
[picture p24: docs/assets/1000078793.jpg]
  
</div>

Observations:

* Prototype was easy to assemble, relatively similar to the last version with now more components.
* Motor was significantly more powerful, and I had to end up holding it down while I was doing my testing initially.
* Despite placing the motor horizontally in an effort to reduce the vertical attentuation, there was still significant vertical movement in the objects and the table I was testing on. A litle bit of vertical vibrations was to be expected and in fact, welcome, due to the fact the objects had to rotate up. 
* The objects made it about 1/4 of the way up before the vibrations were bouncing up and down way too much, and would either fall back down the ramp or fly out of the bowl. 
* After trying several voltages (ranging from 3.3V to 9V), the same things occured, which means that the concept is inherently limited.

Post-Test Actions:

* I don't have too much knowledge of vibrations and dampening apart from a spring mass damper system that I was taught in controls class. 
* I was expecting a concept that seemed easy to tune and get working to be very plug and play, when in fact, there are a lot more factors that go into the design than was expected.
* To try to fix the issue, I went online and tried to research what could be done with the motor placement. All I found was that the angle that it is placed at matters, but that is something that has to be extensively tested with the setup I have currently.

Conclusions:

* This concept has potential to work, however, it would either require: 
    1. Extensive testing on my side
    2. Another person to be working alongside me to solely focus on tuning my current setup (ideally someone with more knowledge than me on the matter)
    3. A complete design overhaul of something that has nothing to do with either object detection, object sorting, or playing with more YOLO models

Path Forward:

Based on the conclusions and the results of the testing, it is best to go down a different concept path that has more potential to be proven and to redefine the scope of the project. While object feeding would be nice, it is NOT a necessary part to get a minimum viable product up and running. Despite the system not auto feeding, I believe that something like this can still reduce object sorting times, and there is scope for object feeding to be added.

Because of what is mentioned above, this concept is now deemed *shelved* and is put aside for an unspecified amount of time, and will most likely be revisited when drawing conclusions for the overall project.

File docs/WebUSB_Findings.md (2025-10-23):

## **Brief Intro**

This page outlines the basics of WebUSB, and how I set it up and tested for basic functionality. It also outlines my conclusion, which was presented on the [Architecture](architecture.md) page.

WebUSB is an API that allows certain compatible microcontrollers to be able to communicate to a web browser. This would open up the potential for users to be able to interact with the Arduino using an HTML file. 

This relates to the project, as it is possible to be able to have a videofeed and have the user see what is going on and allow for a bit of manual control.

This guide has some demos as well as code that can be ran to ensure that WebUSB is working as expected. The following is an adapted version of the tutorials presented in [this video](https://www.youtube.com/watch?v=G8AUgwZCe_Q). For more information about the code and details about WebUSB, watch the linked video. 

## **Demos**

1. USB Recognition
2. Microcontroller to Web Browser Communication
3. Web Browser to Microcontroller Communication

### **USB Recognition**
The goal of this demo is to create a basic website that will allow the user to plug in a USB device and obtain important details to the console. This demo does not require the use of the WebUSB library, and no code needs to be uploaded to the microcontroller. This means that ANY device, regardless of whether it supports WebUSB or not, can run this test successfully, as this relies on the browser picking up the fact that a USB was plugged in rather than communicating with it.

``` html title="USB_recog.html" linenums="1"
<a href="#" id="click">Connect to USB Device</a>

<script>
click.onclick = function() {
    navigator.usb.requestDevice( {filters: [
        {'vendorId': 0x2341}
    ]})
    .then(device => {
        console.log(device)
        console.log("Product Name: " + device.productName.toString(16))
        console.log("Product ID: " + device.productId.toString(16))
        console.log("Vendor ID: "+ device.vendorId.toString(16))
    })
    .catch(error => {
        console.log(error)
    })
}
</script>
```

Images below show output of html code and how it works when an Arduino Leonardo is connected:

HTML Output

HTML Output with Serial

Note that no code is needed for the Arduino.

### **Microcontroller to Web Browser Communication**
The goal of this demo is to be able to send data from the microcontroller and the website. While this demo will work in this particular way, it sets up the backbone for establishing a 2 way communication between the microcontroller and the website.

HTML Code:

``` html title="Leo_to_Web.html" linenums="1"
<!DOCTYPE html>
<html>
    <head>
        <title>USB Communication Test</title>
    </head>
    <body>
        <a href="#" id="click">Listen to Leo</a>
        <button id="connect">Connect</button>
        
        <script src="serial.js"></script>
        
        <script>
            document.getElementById('click').onclick = function() {
                navigator.usb.requestDevice({ filters: [{ 'vendorId': 0x2341 }] })
                    .then(device => {
                        console.log(device);
                        console.log("Product Name: " + device.productName);
                        console.log("Product ID: " + device.productId.toString(16));
                        console.log("Vendor ID: " + device.vendorId.toString(16));
                        console.log("Device Found! Awaiting messages...");
                    })
                    .catch(error => {
                        console.log(error);
                    });
            };

            var port;
            var connectButton = document.getElementById('connect');
            var textDecoder = new TextDecoder();
            var textEncoder = new TextEncoder();

            connectButton.addEventListener('click', function() {
              if (port) {
                    // If port is already connected, disconnect it
                    connectButton.textContent = 'Connect';
                    port.disconnect();
                    port = null;
                    console.log('Device is disconnected.');
                } else {
                    // If there is no port, then connect to a new port
                    serial.requestPort().then(selectedPort => {
                        port = selectedPort;
                        port.connect().then(() => {
                            console.log('Device is connected to Product ID: ' + port.device_.productId.toString(16) + ' and Vendor ID: ' + port.device_.vendorId.toString(16));

                            connectButton.textContent = 'Disconnect';
                            port.onReceive = data => {
                                console.log(textDecoder.decode(data));
                            };
                            port.onReceiveError = error => {
                                console.log('Receive error: ' + error);
                            };
                        }, error => {
                            console.log('Connection error: ' + error);
                        });
                    }).catch(error => {
                        console.log('Connection error: ' + error);
                    });
                }
            });

            serial.requestPort = function() {
                const filters = [
                    { 'vendorId': 0x2341 }
                ];
                return navigator.usb.requestDevice({ 'filters': filters }).then(
                    device => new serial.Port(device)
                );
            };
        </script>
    </body>
</html>
```

Arduino Code:

``` cpp title="Leo2.ino" linenums="1"
#include <WebUSB.h>

// Modified from example https://webusb.github.io/arduino/demos/console
WebUSB WebUSBSerial(1, "webusb.github.io/arduino/demos/console");
int c = 0;

void setup() {
  WebUSBSerial.begin(9600);
  while (!WebUSBSerial) {}
  delay(100);
}

void loop() {
  c = c + 1;
  if (WebUSBSerial){
    WebUSBSerial.println(c);
    WebUSBSerial.flush();    
  } else {
    c = 0;
  }

  delay(1000);
}
```

Serial.js code:

``` js title="serial.js" linenums="1"
var serial = {};

(function() {
  'use strict';

  serial.getPorts = function() {
    return navigator.usb.getDevices().then(devices => {
      return devices.map(device => new serial.Port(device));
    });
  };

  serial.requestPort = function() {
    const filters = [
      { 'vendorId': 0x2341, 'productId': 0x8036 }, // Arduino Leonardo
      { 'vendorId': 0x2341, 'productId': 0x8037 }, // Arduino Micro
      { 'vendorId': 0x2341, 'productId': 0x804d }, // Arduino/Genuino Zero
      { 'vendorId': 0x2341, 'productId': 0x804e }, // Arduino/Genuino MKR1000
      { 'vendorId': 0x2341, 'productId': 0x804f }, // Arduino MKRZERO
      { 'vendorId': 0x2341, 'productId': 0x8050 }, // Arduino MKR FOX 1200
      { 'vendorId': 0x2341, 'productId': 0x8052 }, // Arduino MKR GSM 1400
      { 'vendorId': 0x2341, 'productId': 0x8053 }, // Arduino MKR WAN 1300
      { 'vendorId': 0x2341, 'productId': 0x8054 }, // Arduino MKR WiFi 1010
      { 'vendorId': 0x2341, 'productId': 0x8055 }, // Arduino MKR NB 1500
      { 'vendorId': 0x2341, 'productId': 0x8056 }, // Arduino MKR Vidor 4000
      { 'vendorId': 0x2341, 'productId': 0x8057 }, // Arduino NANO 33 IoT
      { 'vendorId': 0x239A }, // Adafruit Boards!
    ];
    return navigator.usb.requestDevice({ 'filters': filters }).then(
      device => new serial.Port(device)
    );
  }

  serial.Port = function(device) {
    this.device_ = device;
    this.interfaceNumber_ = 2;  // original interface number of WebUSB Arduino demo
    this.endpointIn_ = 5;       // original in endpoint ID of WebUSB Arduino demo
    this.endpointOut_ = 4;      // original out endpoint ID of WebUSB Arduino demo
  };

  serial.Port.prototype.connect = function() {
    let readLoop = () => {
      this.device_.transferIn(this.endpointIn_, 64).then(result => {
        this.onReceive(result.data);
        readLoop();
      }, error => {
        this.onReceiveError(error);
      });
    };
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

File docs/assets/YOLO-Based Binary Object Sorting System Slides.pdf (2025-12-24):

# YOLO-Based Binary Object Sorting System

An AI-Powered Cyber-Physical Prototype for Intelligent Object Classification

Sidh Gurnani

# The Problem

## Inefficient Manual Sorting Processes


- Current manual sorting processes in certain sectors are time-consuming and labor-intensive
- There are limited ‘plug and play’ options
- Sorting processes require lots of time and resources to develop for one specific application
- Possible applications include (not limited to):
- Manufacturing (electronic components, hardware)
- Agriculture (varying bean sizes/types)
- Crime Scene Investigation (bullet casings)
- Everyday use (LEGOs, coins, etc)

# The Solution

## AI-Powered Binary Sorting System

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

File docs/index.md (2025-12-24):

# YOLO-Based Binary Object Sorting System

Welcome! This mkdocs page will contain documentation regarding what this project is about as well as progress for where I am at and all developments that have occured. This serves as a log of information I have collected throughout the development process.

I just want to give a special thank you to Dr. Nirav Merchant from the University of Arizona for being an incredible mentor throughout the whole project.
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

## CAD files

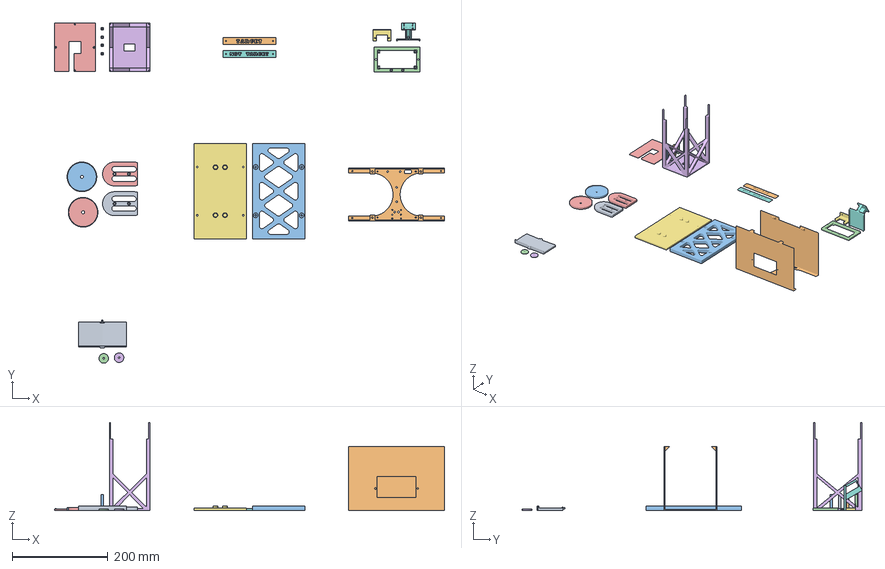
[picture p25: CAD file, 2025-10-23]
docs/assets/YOLO Object Sorter Version 2.0.3mf
814.2 x 710.6 x 184.0 mm
Platform +Shaft - Part 1.stl
Lid - Part 1.stl
Base Platform - Part 1.stl
Cup Washer.stl x 2
Cup -Drawer- (x2) - Part 1.stl x 2
Bottom Sorting Plate - Part 1.stl
Platform End Shaft Holder - Part 1.stl
Cup Labels (Not Labelled).stl x 2
Cup Base (x2) - Part 1.stl x 2
LCD Mounting Panel - Part 1.stl
Camera Holder - Part 1 (1).step
MicroServo 9G (SG90) Mount - Part 1.stl
Corner Camera Holder (x4) - Part 1.step x 4
Camera Lid - Part 1.step

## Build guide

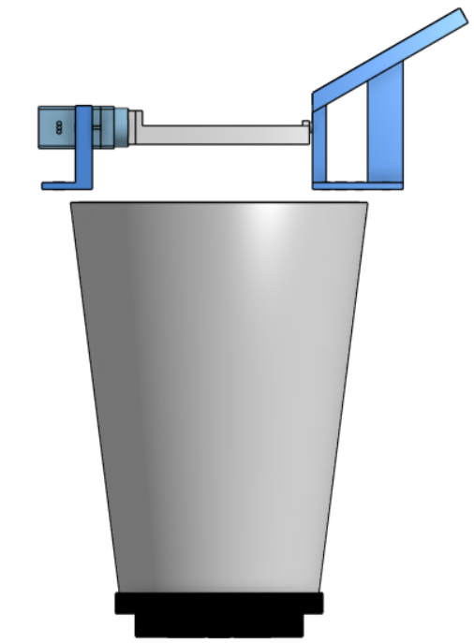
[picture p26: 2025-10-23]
docs/assets/2.1_Sorting_Assembly_6.png

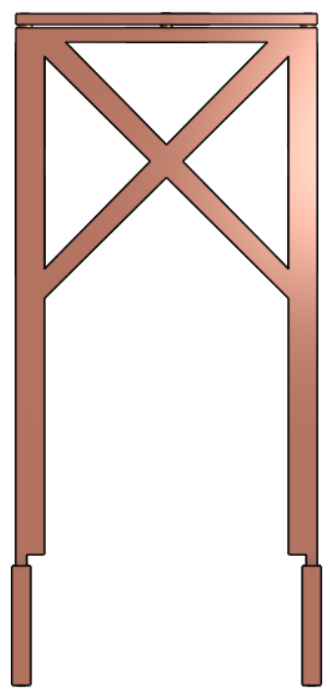
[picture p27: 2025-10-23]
docs/assets/2.1_Camera_Assembly_2.png

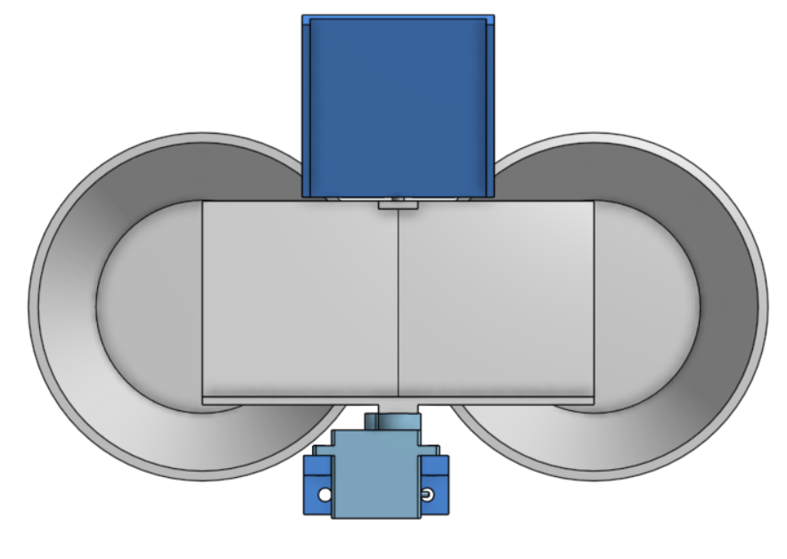
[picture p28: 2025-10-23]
docs/assets/2.1_Sorting_Assembly_5.png

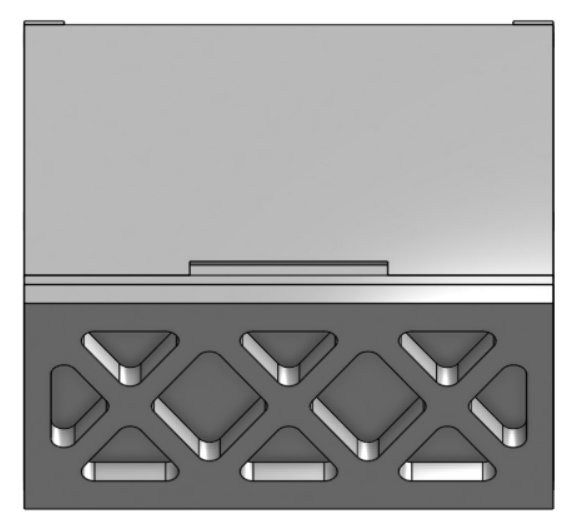
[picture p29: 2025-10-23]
docs/assets/2.1_Body_Assembly_6.png

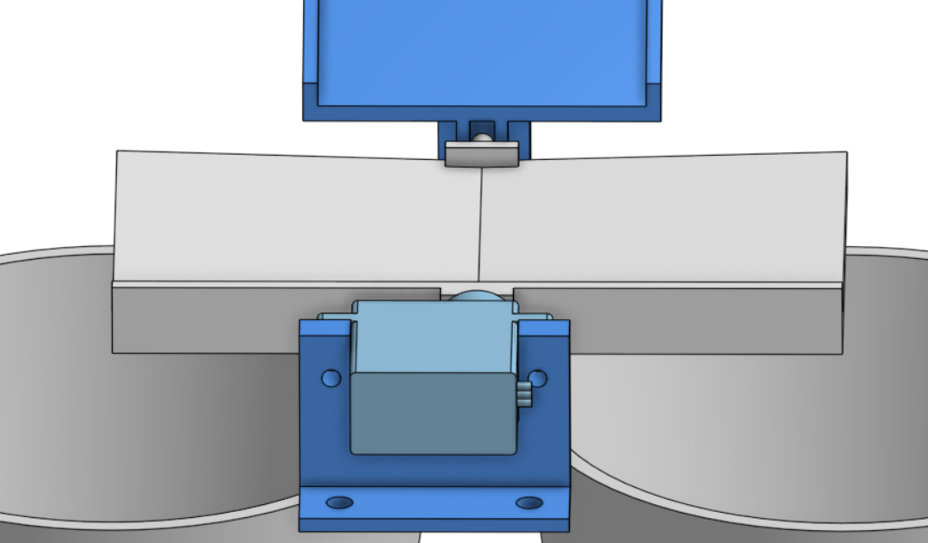
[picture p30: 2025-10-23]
docs/assets/2.1_Sorting_Assembly_7.png

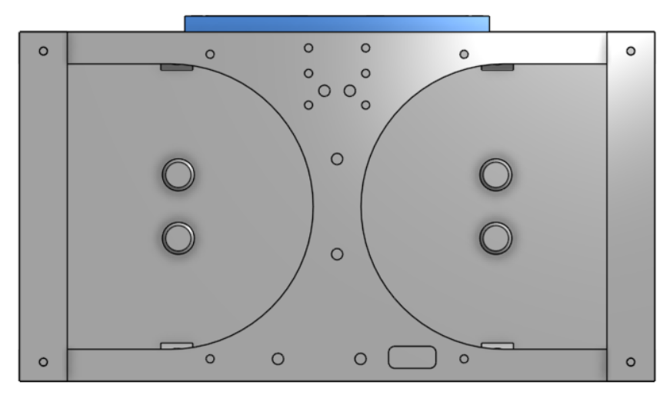
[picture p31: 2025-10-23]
docs/assets/2.1_Body_Assembly_5.png

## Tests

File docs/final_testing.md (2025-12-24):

## Testing Overview

After concluding development of the full cyber physical prototype, testing must be carried out to ensure that it meets the goals that it was intended to, or at least reasonably show that it can do so with further refinement.

One important thing to note here is that the object sorter prototype is NOT optimized for speed. It was tuned entirely with accuracy in mind. With further tuning and refinement, some time can be saved. Areas of refinement include: speeding up the servo, reducing the cooldown, better model training, etc. I will not consider these future improvements as these are more refinements that can be done to enhance and optimize what is already there.

## Test Setup and Scenario

I took some assorted coins I had at home and mixed them up. This pile comprises of pennies, dimes, and quarters. My goal is to be able to use the model trained to be able to sort through this pile.

Throughout the testing I want to answer the following questions:

* How does the prototype compare to a human (myself) when both are binary sorting?
* How does the prototype compare to a human (myself) when the human sorts without limitations?

### Testing Methodology

Below is a list of rules and/or notes regarding the testing methodology:

* Repeatability is required on the most tests to use averages as a baseline rather than relying just on a human being consistent (as humans are consistently inconsistent).
* In general, I will be working at a moderate pace, not too slowly or quickly.
* When I am binary sorting, I will have all objects in a pile, and pull from them one at a time without looking at what I am grabbing from the pile. If the object I select matches what I am looking for, it goes in one pile, and if it does not, it goes into a 'discard' pile. Once the pass has been completed, the discard pile is poured to where the original pile was, and the process is repeated until all objects have been sorted. After sorting, then the objects are counted, written down, and added together to calculate statistics (minus throughput).
* Tests carried out that do not limit the human (myself) will only be ran once to get a picture of the differences rather than averaged. In other words, all non-binary testing done by me will be conducted once to illustrate an obvious and expected difference rather than try to gather any meaningful data.
* When using the prototype, any time spent between passes counts as part of passing, so it is important to ensure that the end user doesn't waste too much time during these downtimes.

### Testing Plan

A pile of coins was chosen to be the test pile. It is the same pile used across all tests (including manual and prototype testing). The pile consists of 15 Quarters, 15 Pennies, 26 Dimes, which yields a total of 56 objects sorted.

1. Human Sorting in Binary Fashion:
    * HSB-1: QUARTER-PENNY-DIME
    * HSB-2: DIME-QUARTER-PENNY
    * HSB-3: PENNY-DIME-QUARTER
    * HSB-A: Average of above 3 trials
2. Human Sorting (No Binary):
    * HSNB-1: Allowed to take one object at a time from big pile, but able to categorize into smaller sorted piles
    * HSNB-2: Allowed to see full pile and sort into smaller sorted piles
3. Prototype Sorting:
    * PS-1
    * PS-2: Recorded on Video (shown below)
    * PS-3: Used supplemental lighting to address any concerns about lighting
    * PS-A: Average of above 3 trials

Bonus Test: How long does it take to filter out the pennies from the whole pile?

1. Prototype (PF-1)
2. Manual (HF-1): Must pull from pile one at a time without looking, determine whether object selected is a penny, then act accordingly
3. Manual (HF-2): Pour entire pile out, then filter out all pennies and everything else

### Benchmarks

* 90% accuracy between actual objects and amount counted (through whichever sorting process was used)
* Object sorter must be faster than the times that a human (myself) sorting in a binary fashion

## Video

<div class="video-wrapper">
  <iframe 
    src="https://www.youtube.com/embed/uLqGxyvlCjE?mute=1&rel=0&playsinline=1"
    title="Trial PS-2"
    frameborder="0"
    allow="autoplay; encrypted-media"
    allowfullscreen>
  </iframe>
</div>

<div><br></div>

## Results

### Speed Comparison

| Test ID | Time (MM:SS) | Throughput (objects/min) |
| --- | --- | --- |
| HSB-1 | 05:36 | 10.00 |
| HSB-2 | 05:18 | 10.56 |
| HSB-3 | 05:29 | 10.21 |
| HSB-A | 05:28 | 10.24 |
| HSNB-1 | 02:41 | 20.87 |
| HSNB-2 | 1:41 | 33.27 |
| PS-1 | 05:01 | 11.16 |
| PS-2 | 04:26 | 12.63 |
| PS-3 | 04:18 | 13.02 |
| PS-A | 04:35 | 12.22 |

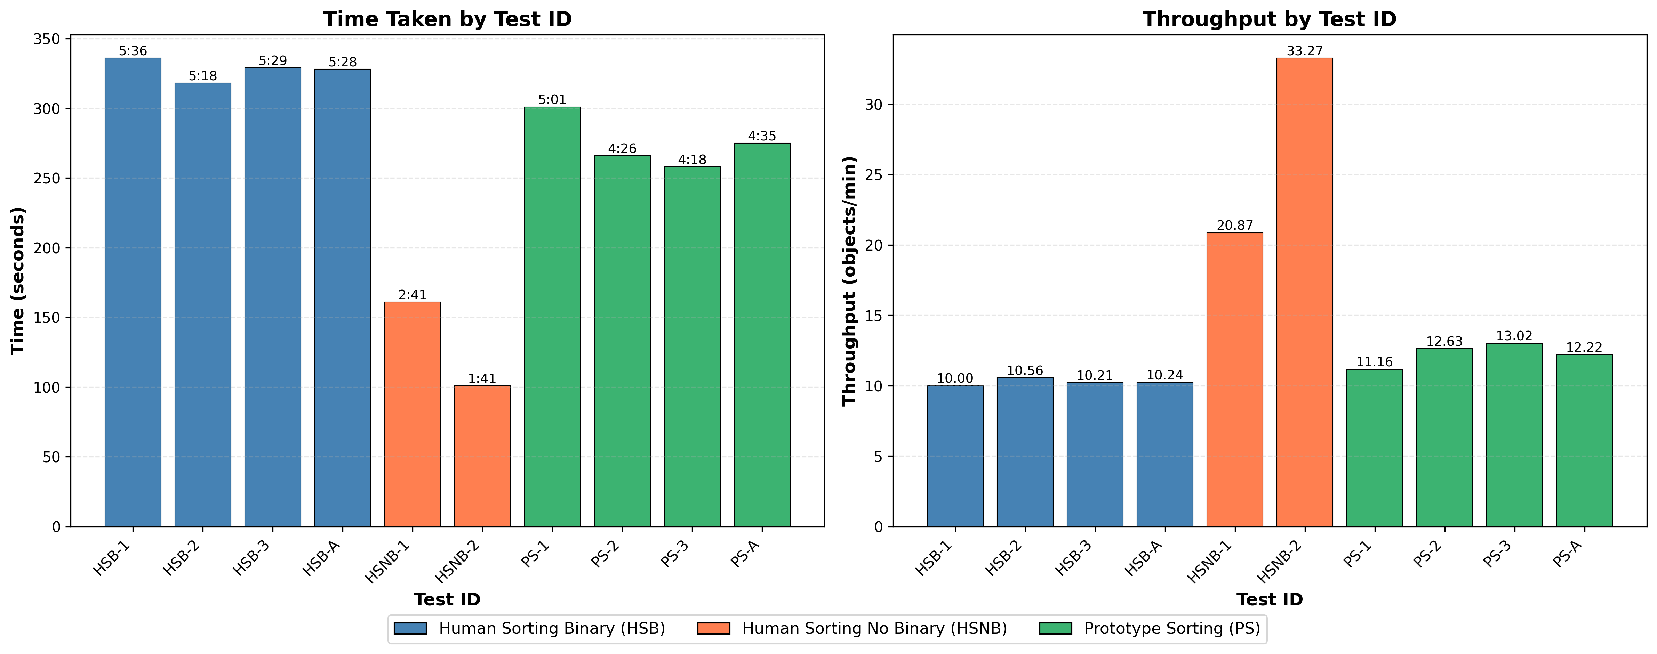
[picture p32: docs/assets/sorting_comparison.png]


Findings:

* Human sorting in a non-binary fashion is BY FAR faster than anything done in a binary fashion.
* Binary sorting done by a human or by the prototype is comparable to one another, and overall, the prototype was about 16% quicker on average. Using HSB-A as a baseline, the prototype was capable of being around 21.3% quicker.
* There is potential to make the prototype faster, especially trimming down the time the servo rotates to either bin and back to the neutral position, however, it is best to minimize risk and ensure it works.

### YOLO Accuracy Per Trial

| Test ID | Pennies Detected | Dimes Detected | Quarters Detected | Type of Error (ACTUAL OBJECT &rarr; DETECTED OBJECT) | Number of Errors | Accuracy | 
| --- | --- | --- | --- | --- | --- | --- |
| PS-1 | 13/15 | 26/26 | 17/15 | Penny &rarr; Dime, Penny &rarr; Quarter, Dime &rarr; Quarter | 3 | 94.6% |
| PS-2 | 14/15 | 22/26 | 20/15 | Penny &rarr; Quarter, Dime &rarr; Quarter (x4) | 5 | 91.1% |
| PS-3 | 16/15 | 27/26 | 13/15 | Quarter &rarr; Dime, Quarter &rarr; Penny, Dime &rarr; Quarter | 3 | 94.6% |

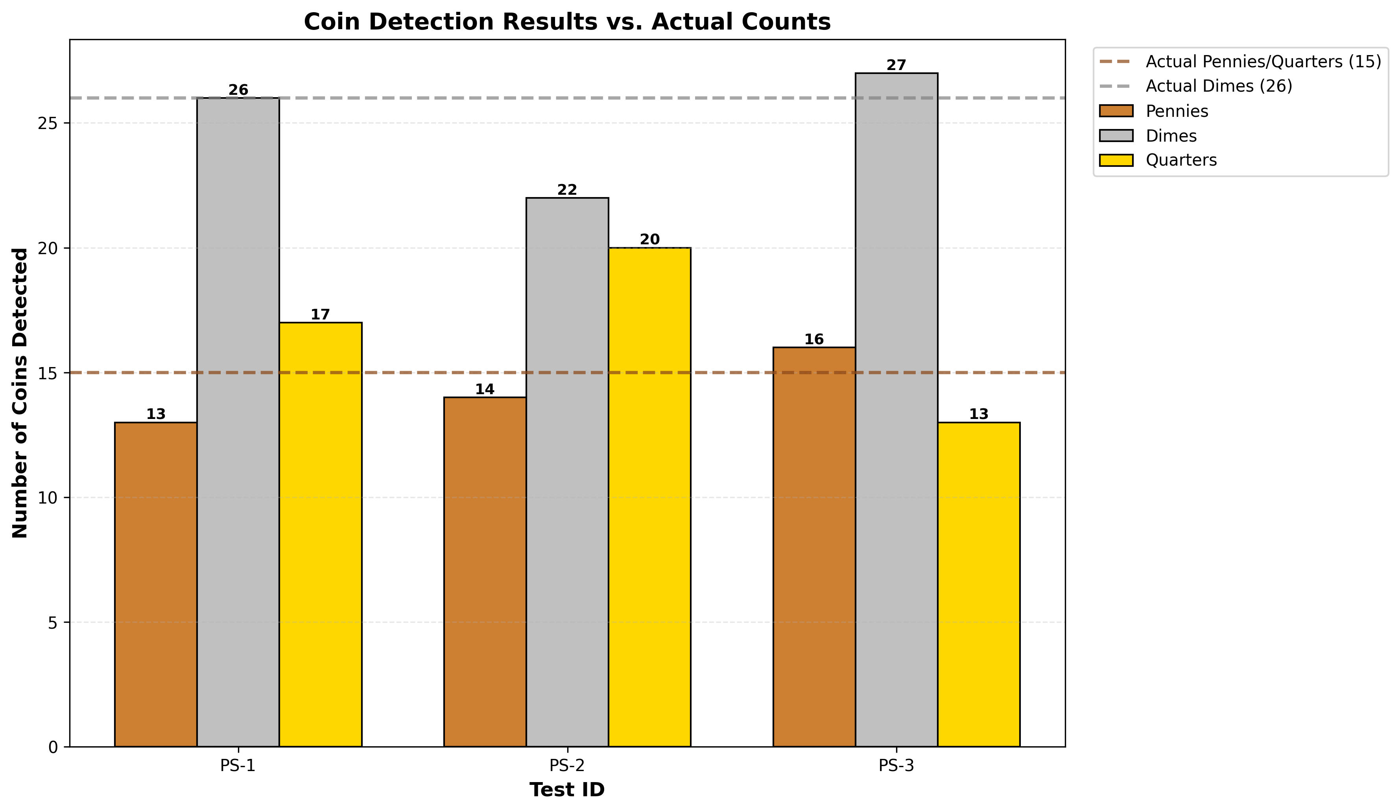
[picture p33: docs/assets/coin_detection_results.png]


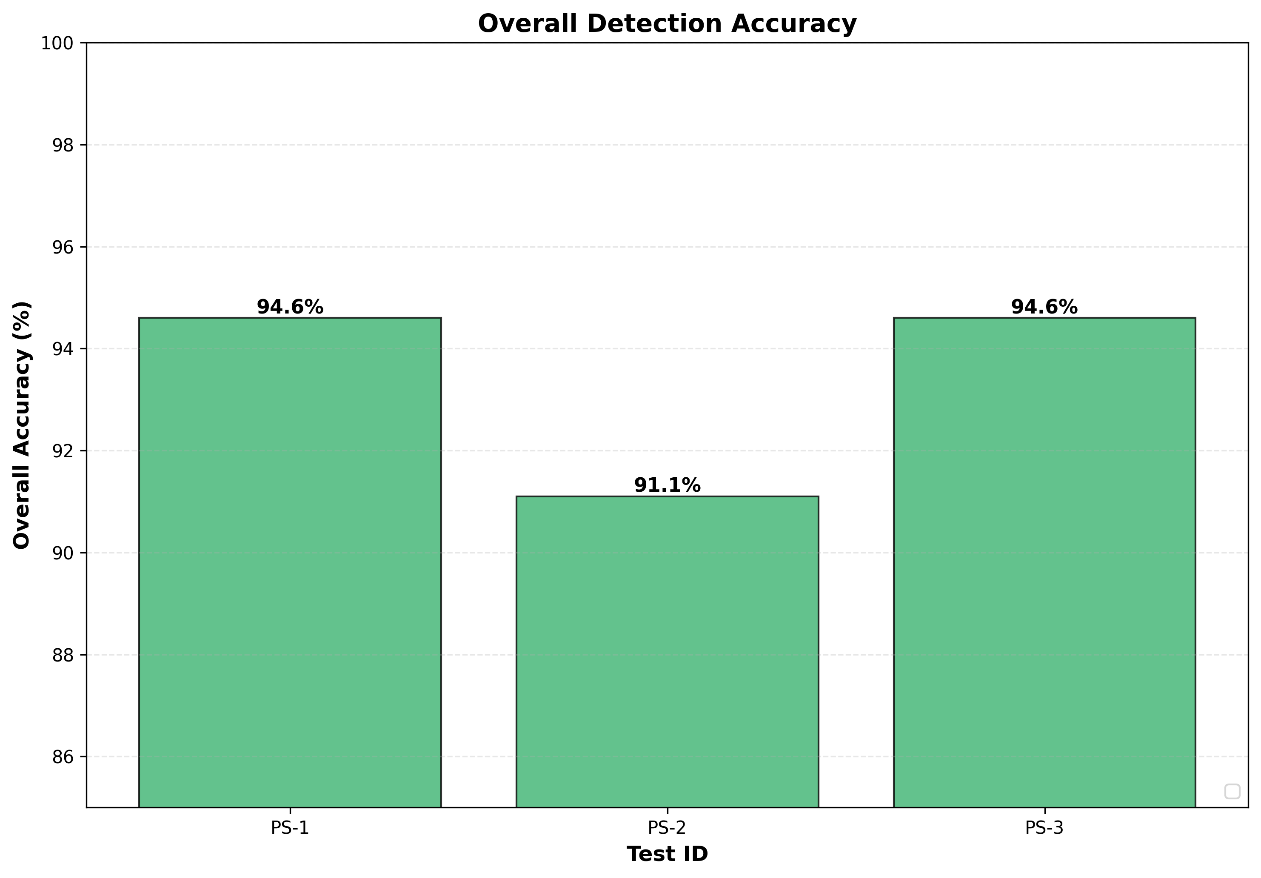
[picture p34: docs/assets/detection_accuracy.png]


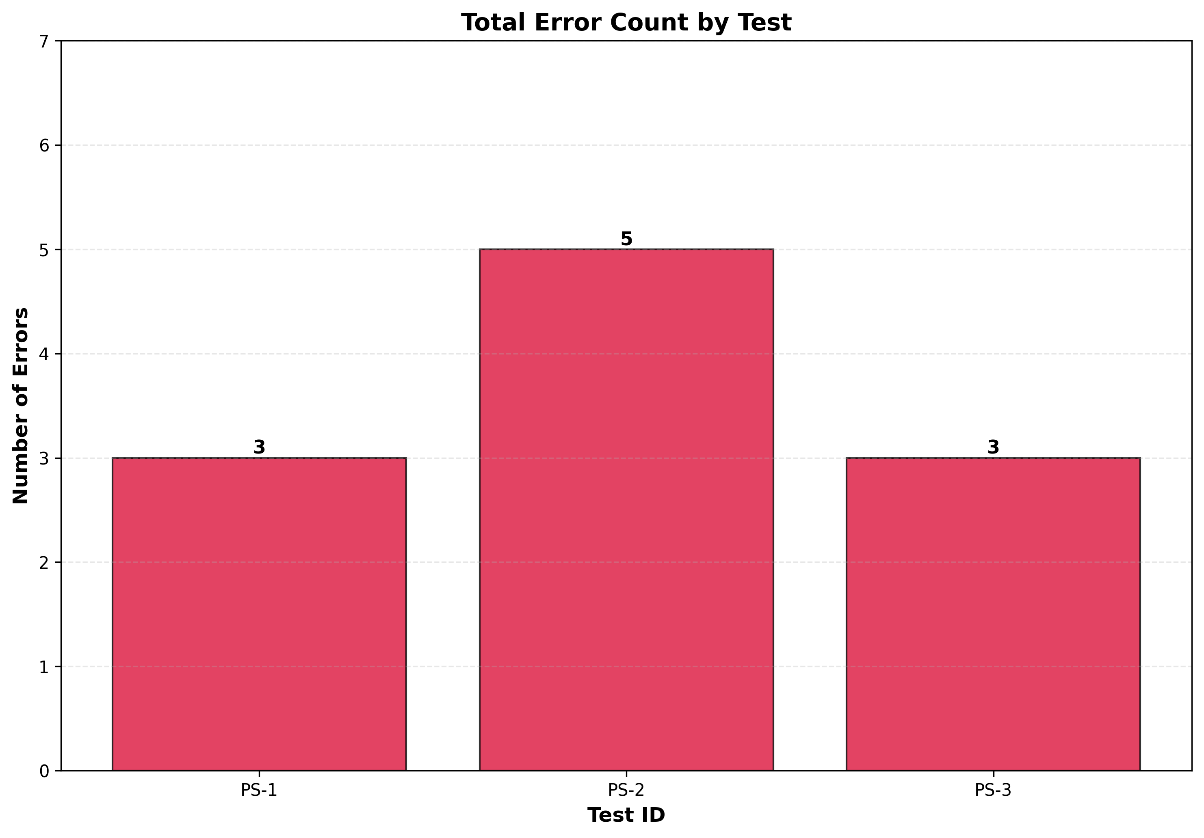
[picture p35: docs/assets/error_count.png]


Findings:

* Pennies and Dimes are fairly strong, with quarters being the weak point
* Detection of quarters led to the most mistakes
* Lighting makes a noticable difference, but overall did not impact the results in the end. On one trial the errors were close to zero but I had to abandon that due to issues with the Arduino.
* Slight overcounting occured in Trial HSB-2, which is as a result of the object getting 'stuck' on the platform due to geometric limitations seen with FDM 3D Printing

### Penny Extraction Test

| Test ID | Time (MM:SS) | Throughput (objects/min) | Notes |
| --- | --- | --- | --- |
| PF-1 | 02:15 | 24.44 | Prototype was 100% accurate in separating pennies |
| HF-1 | 02:23 | 23.07 | Slower than the prototype |
| HF-2 | 00:43 | 76.74 | Humans benefit from global view, but really only applies in situations when global view CAN be utilized (e.g. seeing 1000 resistors for sorting would be tricky) |

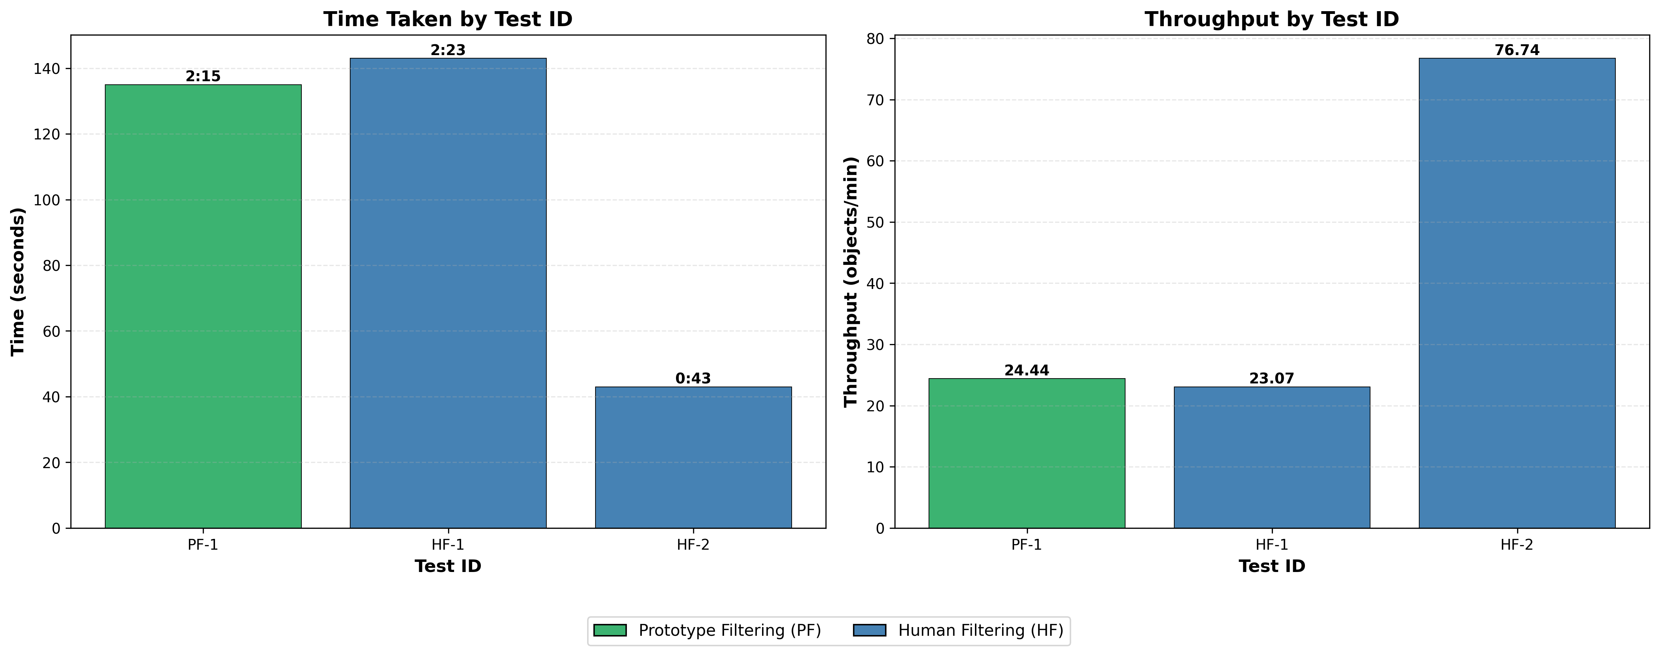
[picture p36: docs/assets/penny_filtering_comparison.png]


## Remarks

Overall, the prototype was markedly faster in binary sorting situations compared against myself. However, humans have the benefit of a global view, which is something that isn't really possible with a YOLO Model. The overarching concept of a binary sorter inherently limited the scope of improvement by quite a bit. 

The speed of the object sorter can be improved in 2 main ways:

1. Improve the model being used. This could also entail swapping the version of YOLO used or trying out a different line of model all together.
2. Reduce the time spent waiting for the object to fall off the platform. If even 0.5 seconds can be saved here, across 50 objects, that would be a full 25 seconds saved, which can be seen as valuable time in a fast-paced environment.

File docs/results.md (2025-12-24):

## General Remarks

Overall, I am satisfied with both aspects of the prototype as is (hardware and software), and it does ultimately serve the purpose that it was designed for. A great proof of concept has been reached and this is something that can be tweaked and applied across various areas. Examples include detecting bullet casings, various kinds of beans, resistors, LEGOs, etc.

If I were to iterate and make a new version, here is what I would do:

1. Software
    * Do more user testing to fix all bugs
    * Tweak Arduino code to ensure it counts total objects instead of total servo sweeps
    * Include relative file paths to make the user experience of setting up the sorting session a lot faster
    * Develop a system to better store data, as having the data stored in excel files is great for smaller scale projects and demos but horrible for large scale implementation
    * Create a few performance modes: conservative, normal, and rapid, all of which adjust the necessary settings to easily speed up and slow down the whole system. As of right now, the user would have to go into the code and find those parameters to change.
    * Create a mode that allows user easily do a dummy run to record a video of objects that need to be sorted (for the purposes of model training). This can be achieved by connecting a button to the Arduino, and if that gets pressed, then do the following: 
        * Start servo from neutral position
        * Sweep to Target in after 3 seconds
        * Sweep back to neutral after 3 seconds
        * Sweep to Not Target after 3 seconds
        * Sweep back to neutral after 3 seconds
        * Repeat until user hits button again
2. Hardware
    * Create channels for wires to easily go through and stay hidden
    * Design a place to hold all electronics that is out of the way from the bins, ideally underneath or somewhere off to the side in a separate 'black box'
    * Redesign some aspects to make it easier to assemble, specifically for tool access
    * Adjust mounting of the LCD to better fit the screen, and maybe hide away the green edge
    * Find a way to mount the potentiometer on the shell to allow for an easy way to adjust screen dimming
    * Design a flashlight mount or add a small strip of LED lights to better illuminate the platform

Here is what I might change if I had to do this all over again:

* **Source a different camera:** The camera used turned out to be pretty poor. The resolution wasn't the greatest, and that led to a harder time detecting complex objects such as coins. I would suggest either using a better camera or even allowing for smartphone compatibility.
* **Design a Web App:** This would allow for such a device to be run on much lower end devices at higher performances, but that would unlock new challenges with communication between the web interface and Arduino.
* **Switch away from a pure binary concept:** If the user knew the number of unique classes beforehand, then it would be entirely possible to have a modular system of bins that allows the number of bins to be specified. From there, only 1 pass would be required to sort through all objects, and would greatly speed up the sorting process. This has potential because during testing, the same working conditions between a human and the prototype always saw the prototype faster at sorting. However, a system with 10 bins would be hard to design. A middle ground is a 3 bin system, where 2 targets are being searched and the rest go to an other bin, which would halve the number of passes required.
* **Conciously slim down the size of the prototype:** While it is simple, the proptotype is rather large, and I think that the size of it can be trimmed down to help reduce filament usage and cost.
* **Better overall camera housing module:** The camera housing module was designed purely from an optimization point of view to use the least amount of filament. However, I would design an enclosed box with bright LED lights that illuminates the area where the objects are being viewed.
* **Platform geometry/size:** The platform itself is a restriction of what types of objects can be sorted. Bigger objects cannot be ran through simply because of the size of the platform.
* **Experiement with a different microcontroller:** Since the web app concept was shelved midway through the project, the need for a WebUSB board was not required. It might have not been a bad idea to experiement with a microcontroller that has an embedded camera to reduce some of the complexities in the design. This might also open up the path to try and use something like TinyML to optimize the sorting process and have it run directly on the microcontroller rather than using a laptop as the brain of the whole operation.
* **Design a system for object feeding:** To improve the user experience further, a system that can feed most kinds of objects should be introduced to make the process more hands-off.

If I were to redesign or continue forth with the project development, I would use the above list as a way to establish a good path forward to continue forth with the development. 

## My take on using GenAI for such projects

Overall, GenAI has been an incredible advancement in technology. The ability to put in what you want to do in words and have a computer translate that into an actual command is a huge leap. However, it does have its limitations, and to say this could be used to generate whole projects is not the best use of GenAI.

GenAI is like a tool, but not a simple tool like a pencil or pen. It is like a swiss army knife, where there are a ton of tools that can be used within this larger tool. In the same way that swiss army knives have knives, screwdrivers, or pliers, GenAI has the ability to interpret long documents, perform deep research, and generate code. No matter how impressive any swiss army knife is, a general contractor won't ask all their employees to start building homes only using swiss army knives. That is exactly the way I see GenAI. 

Even if I had prompted any GenAI model to build a project such as this one, it would not give me a working output at once. I might have to spend time debugging, or tweaking some functions, or maybe I gave it too much freedom in one aspect and too little freedom in another. At the end of the day, whole projects are not built in one step, or one prompt. They require many tools and in most cases, many people along the way. 

I will be transparent and say that I did use GenAI to work through this project, and utilized a combination of OpenAI's ChatGPT and Anthropic's Claude models to work through the project. However, my use of GenAI was purely to help supplement areas where I am not as strong. I did all of the idea generation and CAD on my own, but I used it to help me work through code. Note that I spent the time learning about how to code during my undergrad and again at the start of the project, which helped me immensely with the debugging process as well as sometimes guiding the GenAI model towards a more correct path.

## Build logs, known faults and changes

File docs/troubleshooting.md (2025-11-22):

# Troubleshooting and FAQ

## Troubleshooting Guide

### Hardware Issues

#### Arduino Not Detected
**Symptoms:** "No Arduino detected" error during setup

**Solutions:**

1. Verify Arduino Leonardo is connected via USB
2. Install Arduino drivers if on Windows
3. Check Device Manager for COM port
4. Try different USB cable/port
5. Restart application after connecting Arduino

#### Camera Not Working
**Symptoms:** Black screen or "Camera test FAILED"

**Solutions:**

1. Close other applications using camera (Zoom, Teams, etc.)
2. Try different camera index in wizard
3. Check camera permissions in Windows/macOS settings
4. Verify camera works in another application first
5. Use USB 2.0 port instead of USB 3.0 (sometimes more stable)
6. Unplug and replug the webcam

#### Servo Not Moving
**Symptoms:** Objects detected but not physically sorted

**Solutions:**

1. Check servo is connected to correct pin (default: pin 3)
2. Verify 5V power supply to servo
3. Test servo with simple Arduino sketch first
4. Check TARGET_ANGLE and NOT_TARGET_ANGLE values
5. Ensure servo isn't mechanically blocked

### Software Issues

#### Model Not Loading
**Symptoms:** Error when selecting .pt file

**Solutions:**

1. Verify file is a valid YOLO .pt model
2. Check Python has ultralytics package installed
3. Ensure model is trained for object detection (not classification)
4. Try re-training model with latest Ultralytics YOLO

#### Objects Not Detected
**Symptoms:** Camera shows feed but no detections

**Solutions:**

1. Lower YOLO_CONF_THRESHOLD (try 0.50)
2. Verify model is trained on your object classes
3. Improve lighting conditions
4. Ensure objects are in frame and clearly visible
5. Check object names match exactly (case-sensitive)

#### Communication Timeouts
**Symptoms:** "FATAL: No pass data received" error

**Solutions:**

1. Increase timeout value (currently 3s)
2. Check Arduino Serial Monitor for errors
3. Verify Arduino code uploaded correctly
4. Reset Arduino and reconnect
5. Check for loose USB connection

### Performance Issues

#### Slow Detection
**Symptoms:** Long delays between object detections

**Solutions:**

1. Reduce FRAME_RATE_MS to 100ms
2. Reduce detection_confirmation_frames to 2
3. Lower YOLO_IMG_SIZE to 320 (faster inference)
4. Use CPU with better single-core performance
5. Close other applications

#### High CPU Usage
**Symptoms:** Computer fans loud, system laggy

**Solutions:**

1. Increase FRAME_RATE_MS to 200ms
2. Reduce YOLO_IMG_SIZE to 320
3. Close unnecessary applications
4. Use dedicated GPU if available (CUDA)

#### False Positives
**Symptoms:** Shadows or wrong objects being detected

**Solutions:**

1. Increase YOLO_CONF_THRESHOLD to 0.70
2. Increase detection_confirmation_frames to 4
3. Improve consistent lighting
4. Retrain model with more diverse examples
5. Add negative examples to training data

## FAQ

### General Questions

**Q: How many unique object types can the system sort?**
A: Theoretically unlimited, but practical limit is ~10-15 unique object types due to EEPROM storage and sorting time. Each additional type requires one more pass.

**Q: How accurate is the sorting?**
A: Accuracy depends on model quality, lighting, and object distinctiveness. A properly trained model and a controlled testing and deployment environment can yield an accuracy above 95%.

**Q: How fast can it sort?**
A: Speed heavily depends on servo movement time and detection settings, and partially dependent on the quality of the model being used.

### Technical Questions

**Q: Why does Arduino send PASS_COMPLETE 3 times?**
A: Redundancy to ensure Python receives the message despite potential serial buffer issues.

**Q: What is the detection cooldown for?**
A: Prevents the same object from being counted multiple times as it passes through the camera view.

**Q: Can I use a different Arduino board?**
A: Yes, but must support Serial (not just USB CDC). Leonardo, Mega, and Uno work. Nano has limited EEPROM.

**Q: Why is the first pass total used as ground truth?**
A: The first pass counts ALL objects (target + non-target), providing the true total count before any are removed.
